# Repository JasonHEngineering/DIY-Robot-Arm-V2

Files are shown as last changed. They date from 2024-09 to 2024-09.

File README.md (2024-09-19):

## DIY Robot Arm V2
This repository is for archiving a prior 6 DOF robot project that is no longer maintained.
I am now working on the next V3 version instead. 

### Contents
| Folder  | Contents|
| --- | --- |
| [Adaptor Board](https://github.com/JasonHEngineering/DIY-Robot-Arm-V2/tree/main/Adaptor%20Board%20(schema%2C%20gerbers%2C%20kicad%20project%20folder)) | KiCad Project files. Gerber files for PCB. But no SMD assembly because for this variant of adaptor board, I did the soldering myself using both soldering iron and hot air solder. |
| [Arduino Nano](https://github.com/JasonHEngineering/DIY-Robot-Arm-V2/tree/main/Arduino%20Nano%20(.ino%20file)) | Load this file into Arduino Nano 33 BLE/IoT device. This is to be mounted into adaptor board above. |
| [CAD files](https://github.com/JasonHEngineering/DIY-Robot-Arm-V2/tree/main/CAD%20files%20(2d%2C%20step)) | Step files and 2d drawings. 2d drawings are not fully detailed; mainly the threads and tight tolerances are detailed. |
| [Raspberry Pi](https://github.com/JasonHEngineering/DIY-Robot-Arm-V2/tree/main/Raspberry%20Pi%20(plotly%20dash%20host)) | Python script and dependencies to be run on raspberry Pi 3/4 |

### Mechanical Structure
Machined CNC parts placement in assembly as shown below. 
> [!NOTE]
> In such a setup, micro limit switches can only zero the respective axis angles approximately. Next version shall use absolute encoders.    
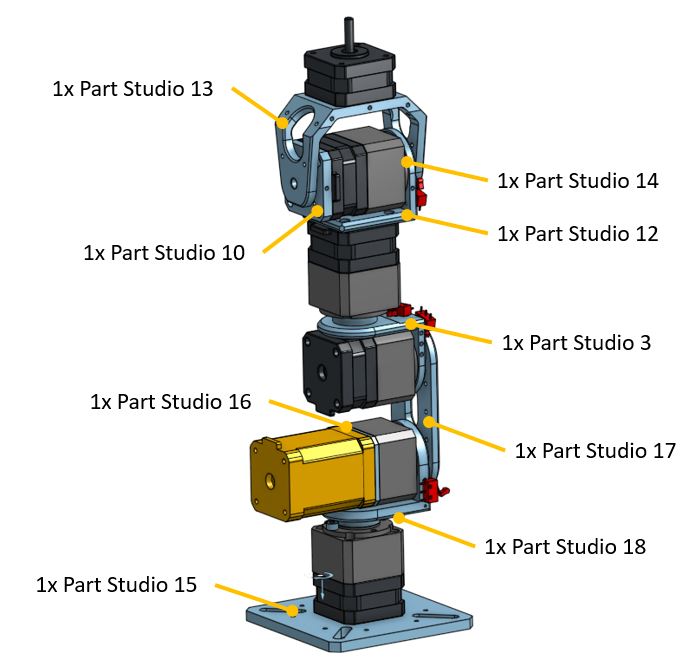
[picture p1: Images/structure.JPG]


Below illustration of user interface dealing with forward kinematics values:  
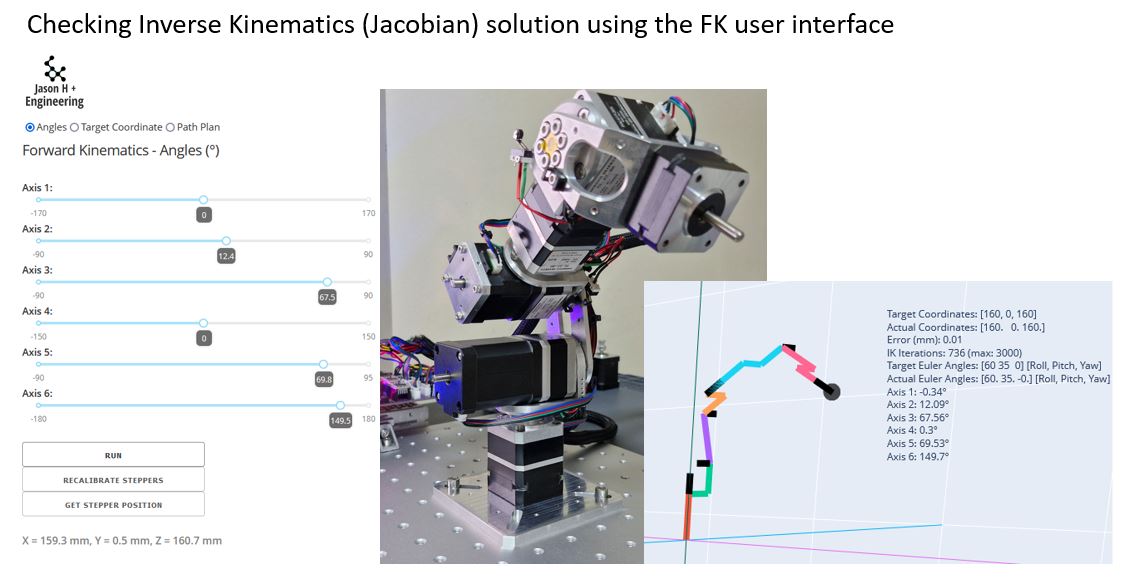
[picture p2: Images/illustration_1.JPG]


### Inverse Kinematics Solver
[Python solver](https://github.com/JasonHEngineering/Inverse-Kinematics)
1. Inverse Kinematics (CCD) – Cyclic Coordinate Descent in 3d space
2. Inverse Kinematics (vector formula Jacobian) - Euler
3. Inverse Kinematics (Numerical Jacobian) - Euler
4. Inverse Kinematics (Numerical Jacobian) - Quaternion

### Quick Illustration at YouTube
DIY Robot Arm V2 (https://www.youtube.com/watch?v=ZaQQ6-Mw-B4)

### Additional Info at WordPress
For more data/info, please refer to this [WordPress page](https://jashuang1983.wordpress.com/robotics-6-dof-arm-v2/).

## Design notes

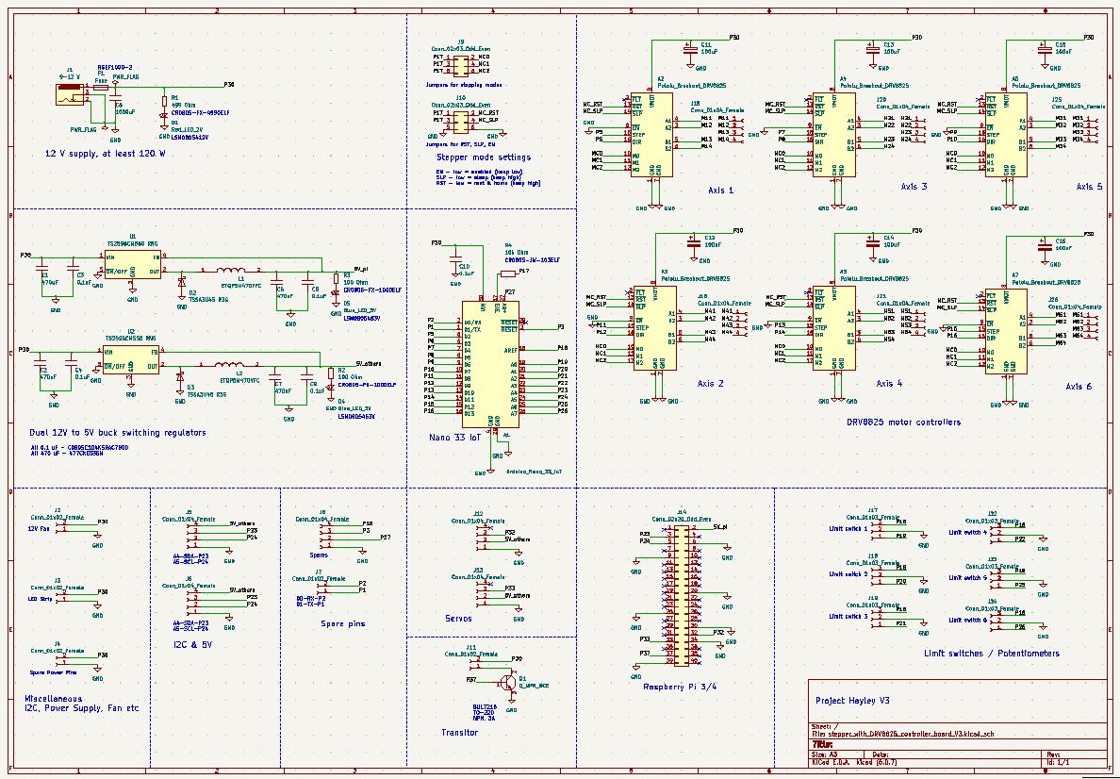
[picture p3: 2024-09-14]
Adaptor Board (schema, gerbers, kicad project folder)/schematic.JPG

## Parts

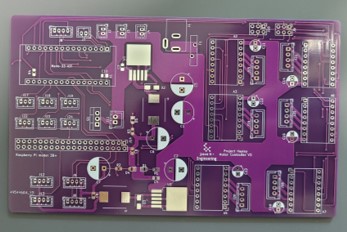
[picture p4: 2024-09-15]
Adaptor Board (schema, gerbers, kicad project folder)/without_components.jpg

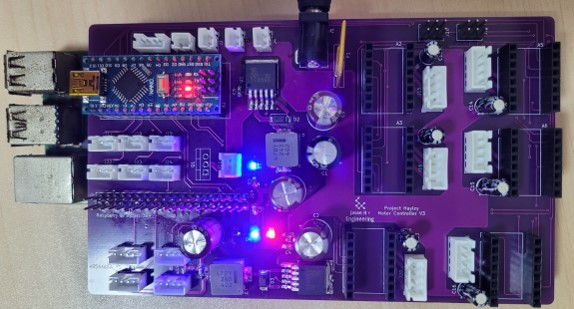
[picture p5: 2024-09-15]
Adaptor Board (schema, gerbers, kicad project folder)/with_components_mounted.jpg

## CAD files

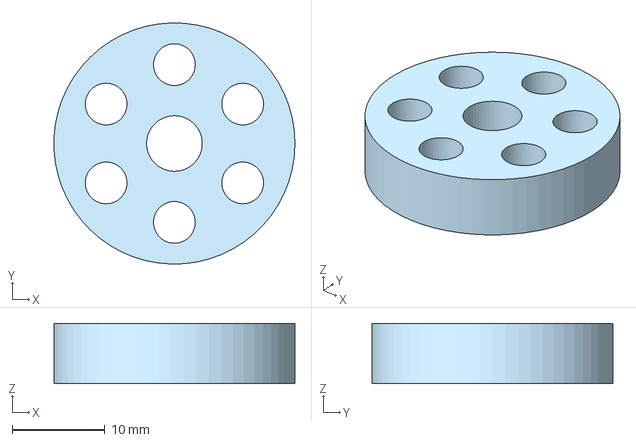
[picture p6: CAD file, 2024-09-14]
CAD files (2d, step)/Part 14.step
26.0 x 26.0 x 6.50 mm

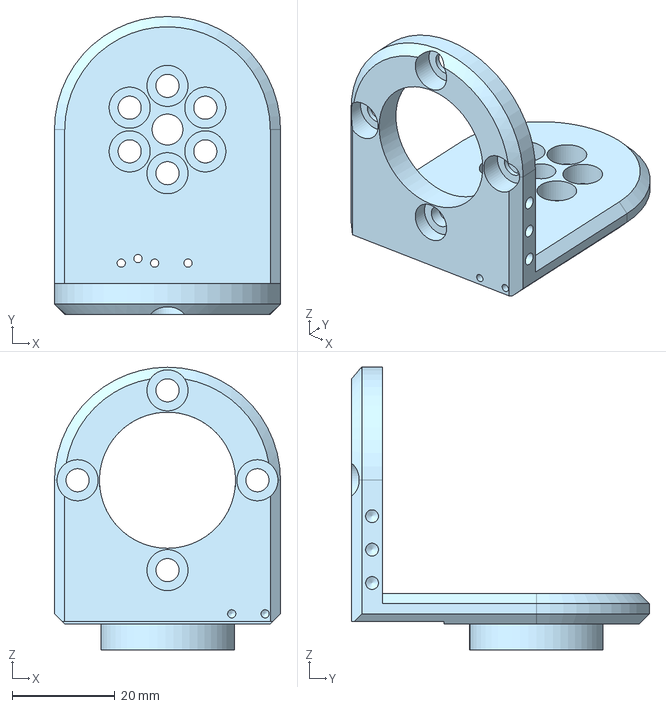
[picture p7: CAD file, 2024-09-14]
CAD files (2d, step)/Part 3.step
44.0 x 58.0 x 55.0 mm

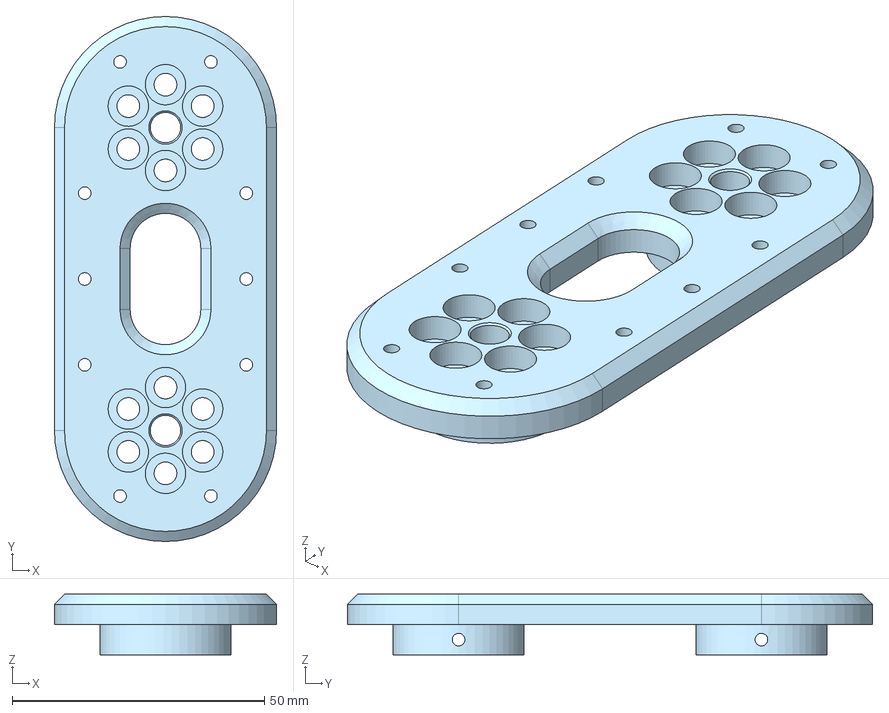
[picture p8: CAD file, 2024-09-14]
CAD files (2d, step)/Part 17.step
44.0 x 104.0 x 12.0 mm

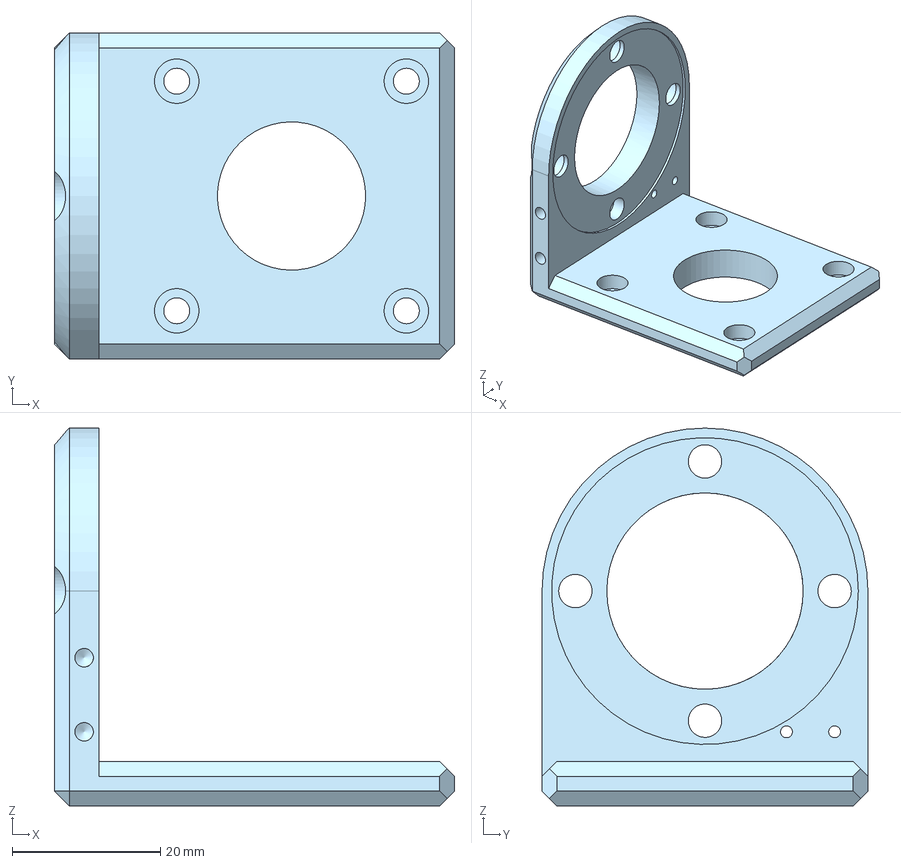
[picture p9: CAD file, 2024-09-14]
CAD files (2d, step)/Part 12.step
54.0 x 44.0 x 51.0 mm

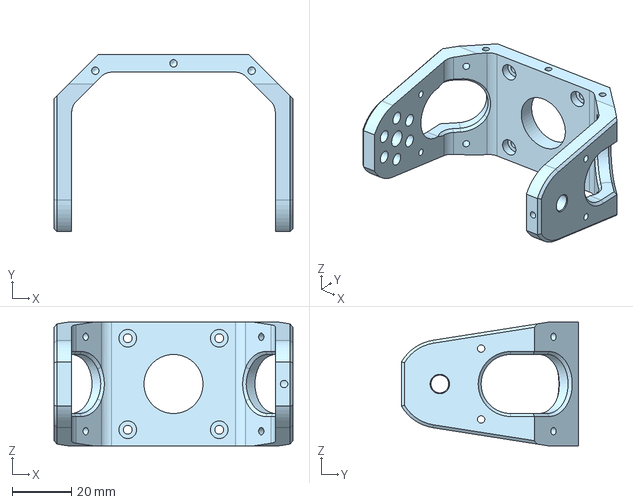
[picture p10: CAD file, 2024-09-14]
CAD files (2d, step)/Part 13.step
81.0 x 60.0 x 42.0 mm

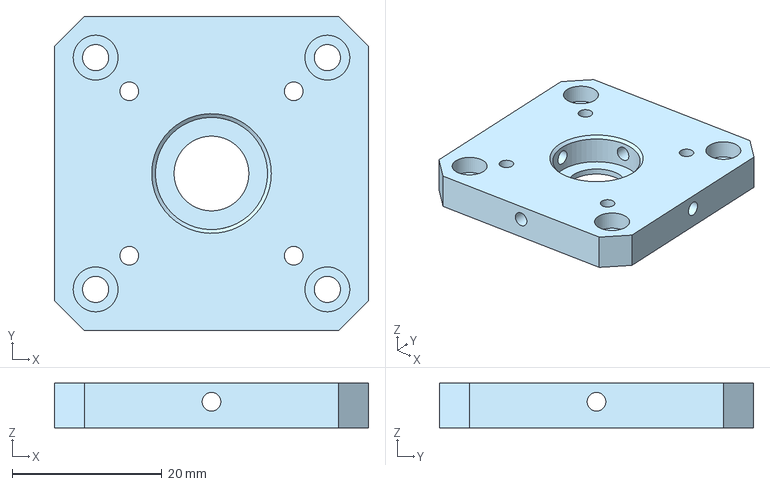
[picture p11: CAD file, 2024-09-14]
CAD files (2d, step)/Part 10.step
42.0 x 42.0 x 6.00 mm

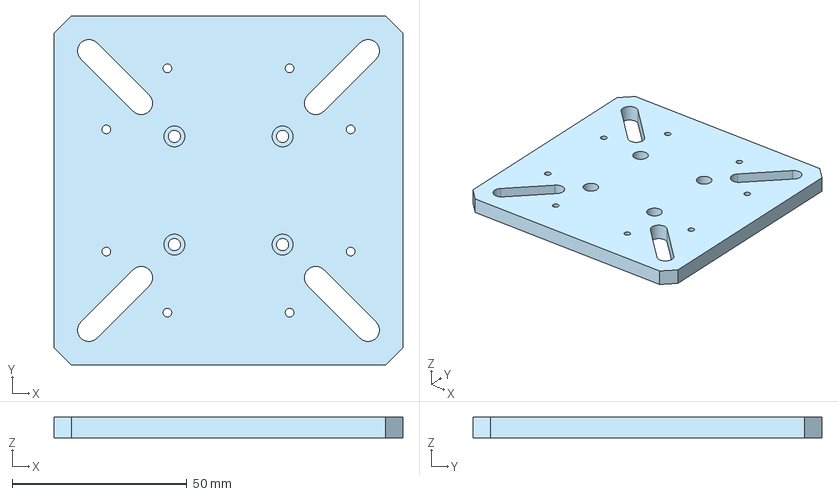
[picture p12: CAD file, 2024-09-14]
CAD files (2d, step)/Part 15.step
100.0 x 100.0 x 6.00 mm

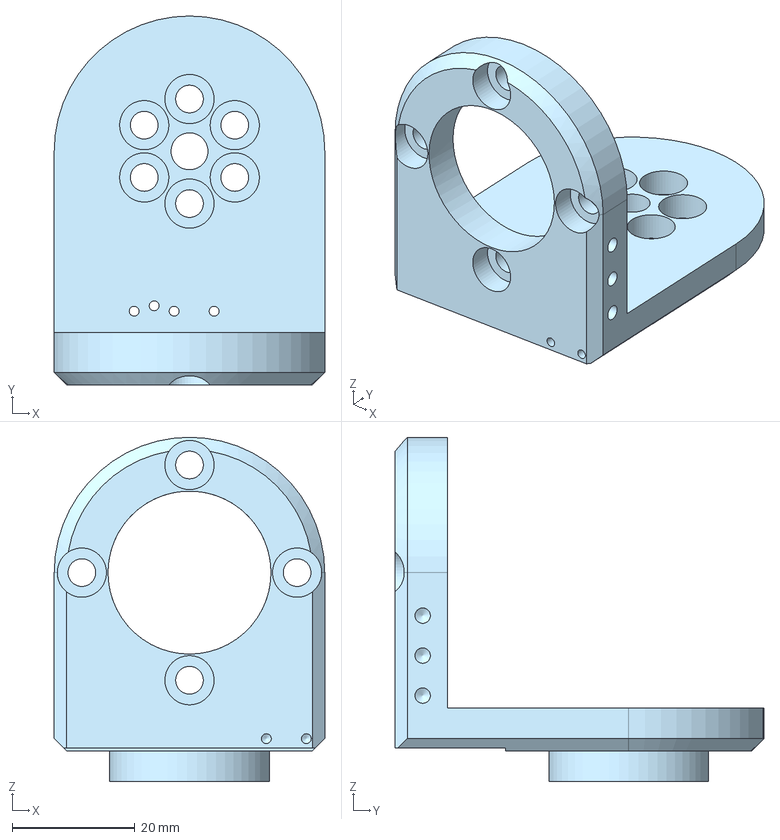
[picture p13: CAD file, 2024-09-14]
CAD files (2d, step)/Part 18.step
44.0 x 60.0 x 56.0 mm

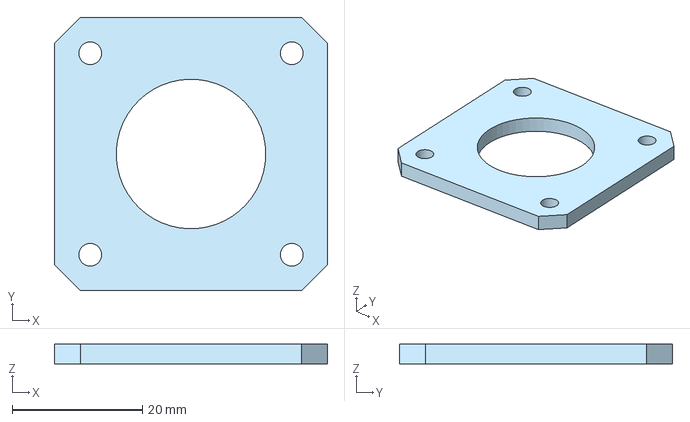
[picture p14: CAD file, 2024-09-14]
CAD files (2d, step)/Part 16.step
42.0 x 42.0 x 3.00 mm

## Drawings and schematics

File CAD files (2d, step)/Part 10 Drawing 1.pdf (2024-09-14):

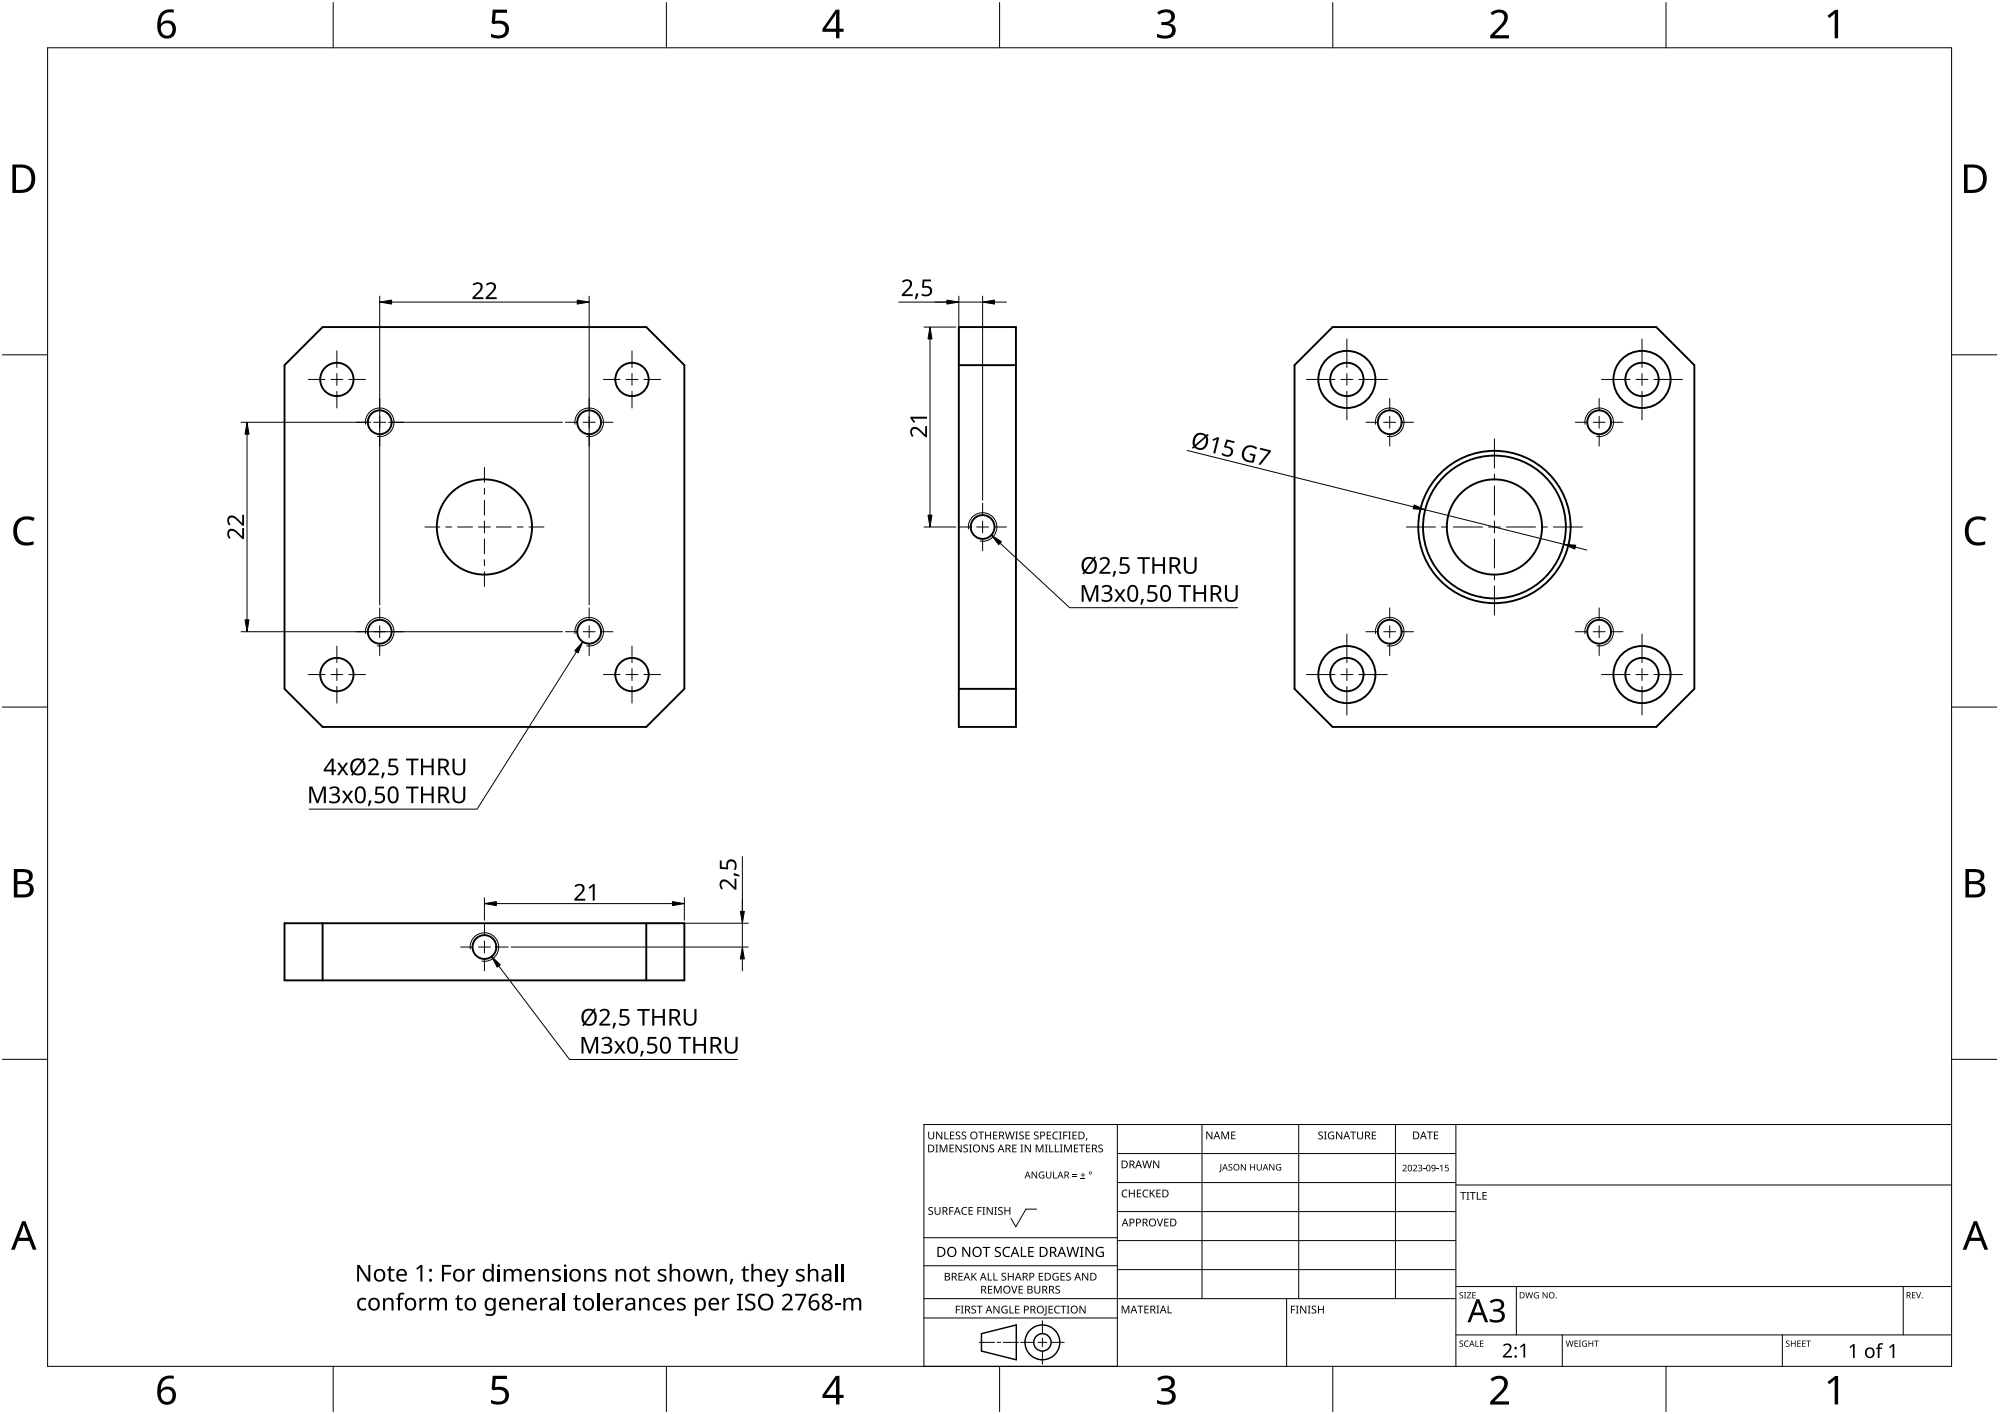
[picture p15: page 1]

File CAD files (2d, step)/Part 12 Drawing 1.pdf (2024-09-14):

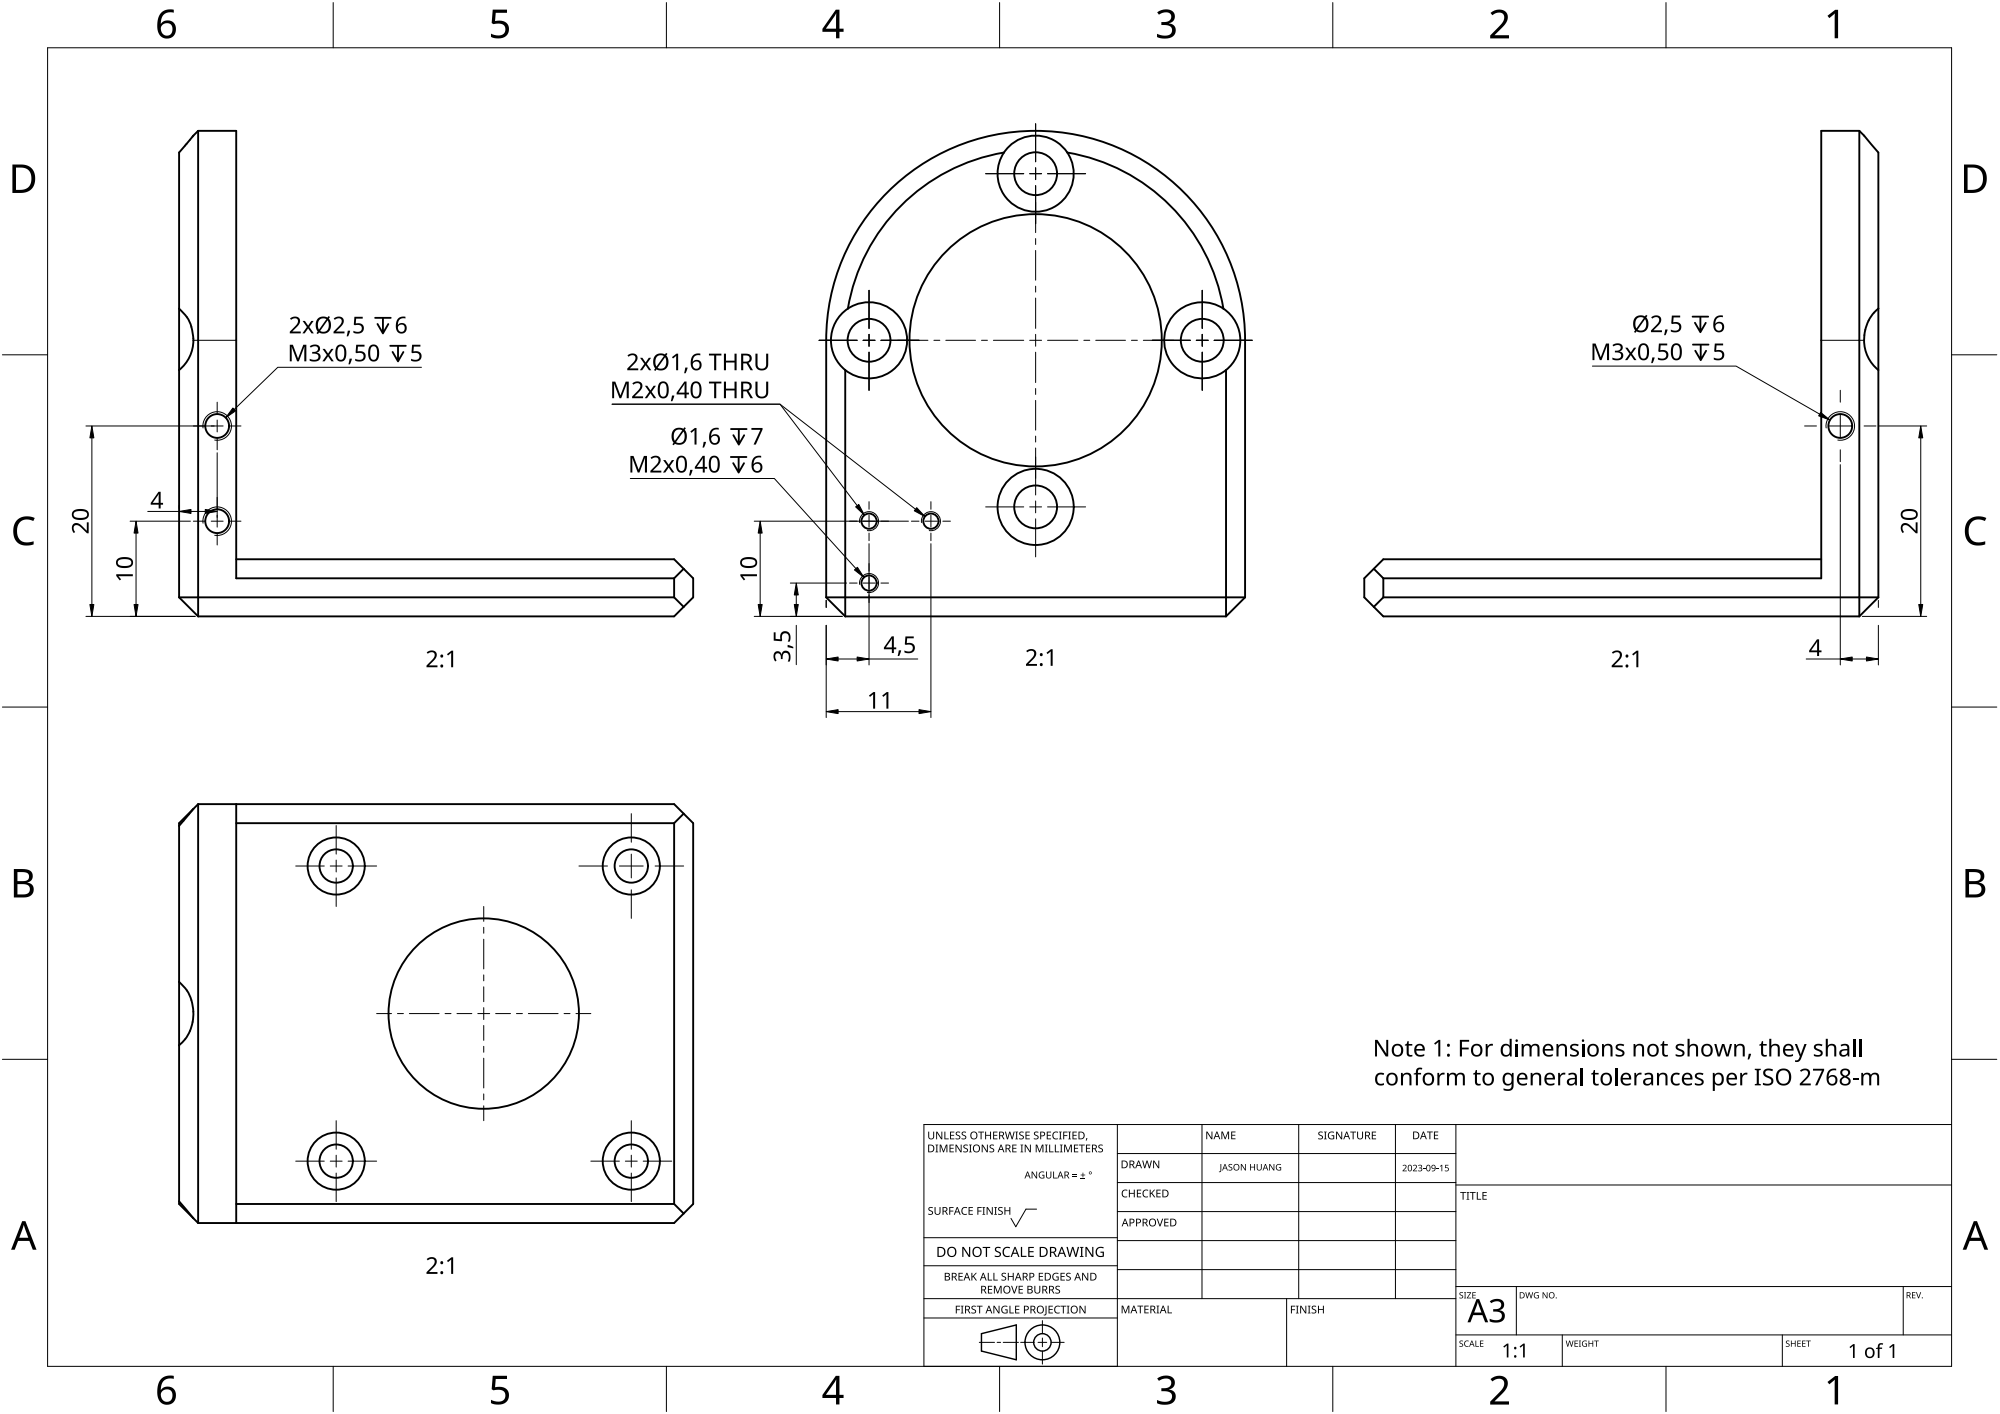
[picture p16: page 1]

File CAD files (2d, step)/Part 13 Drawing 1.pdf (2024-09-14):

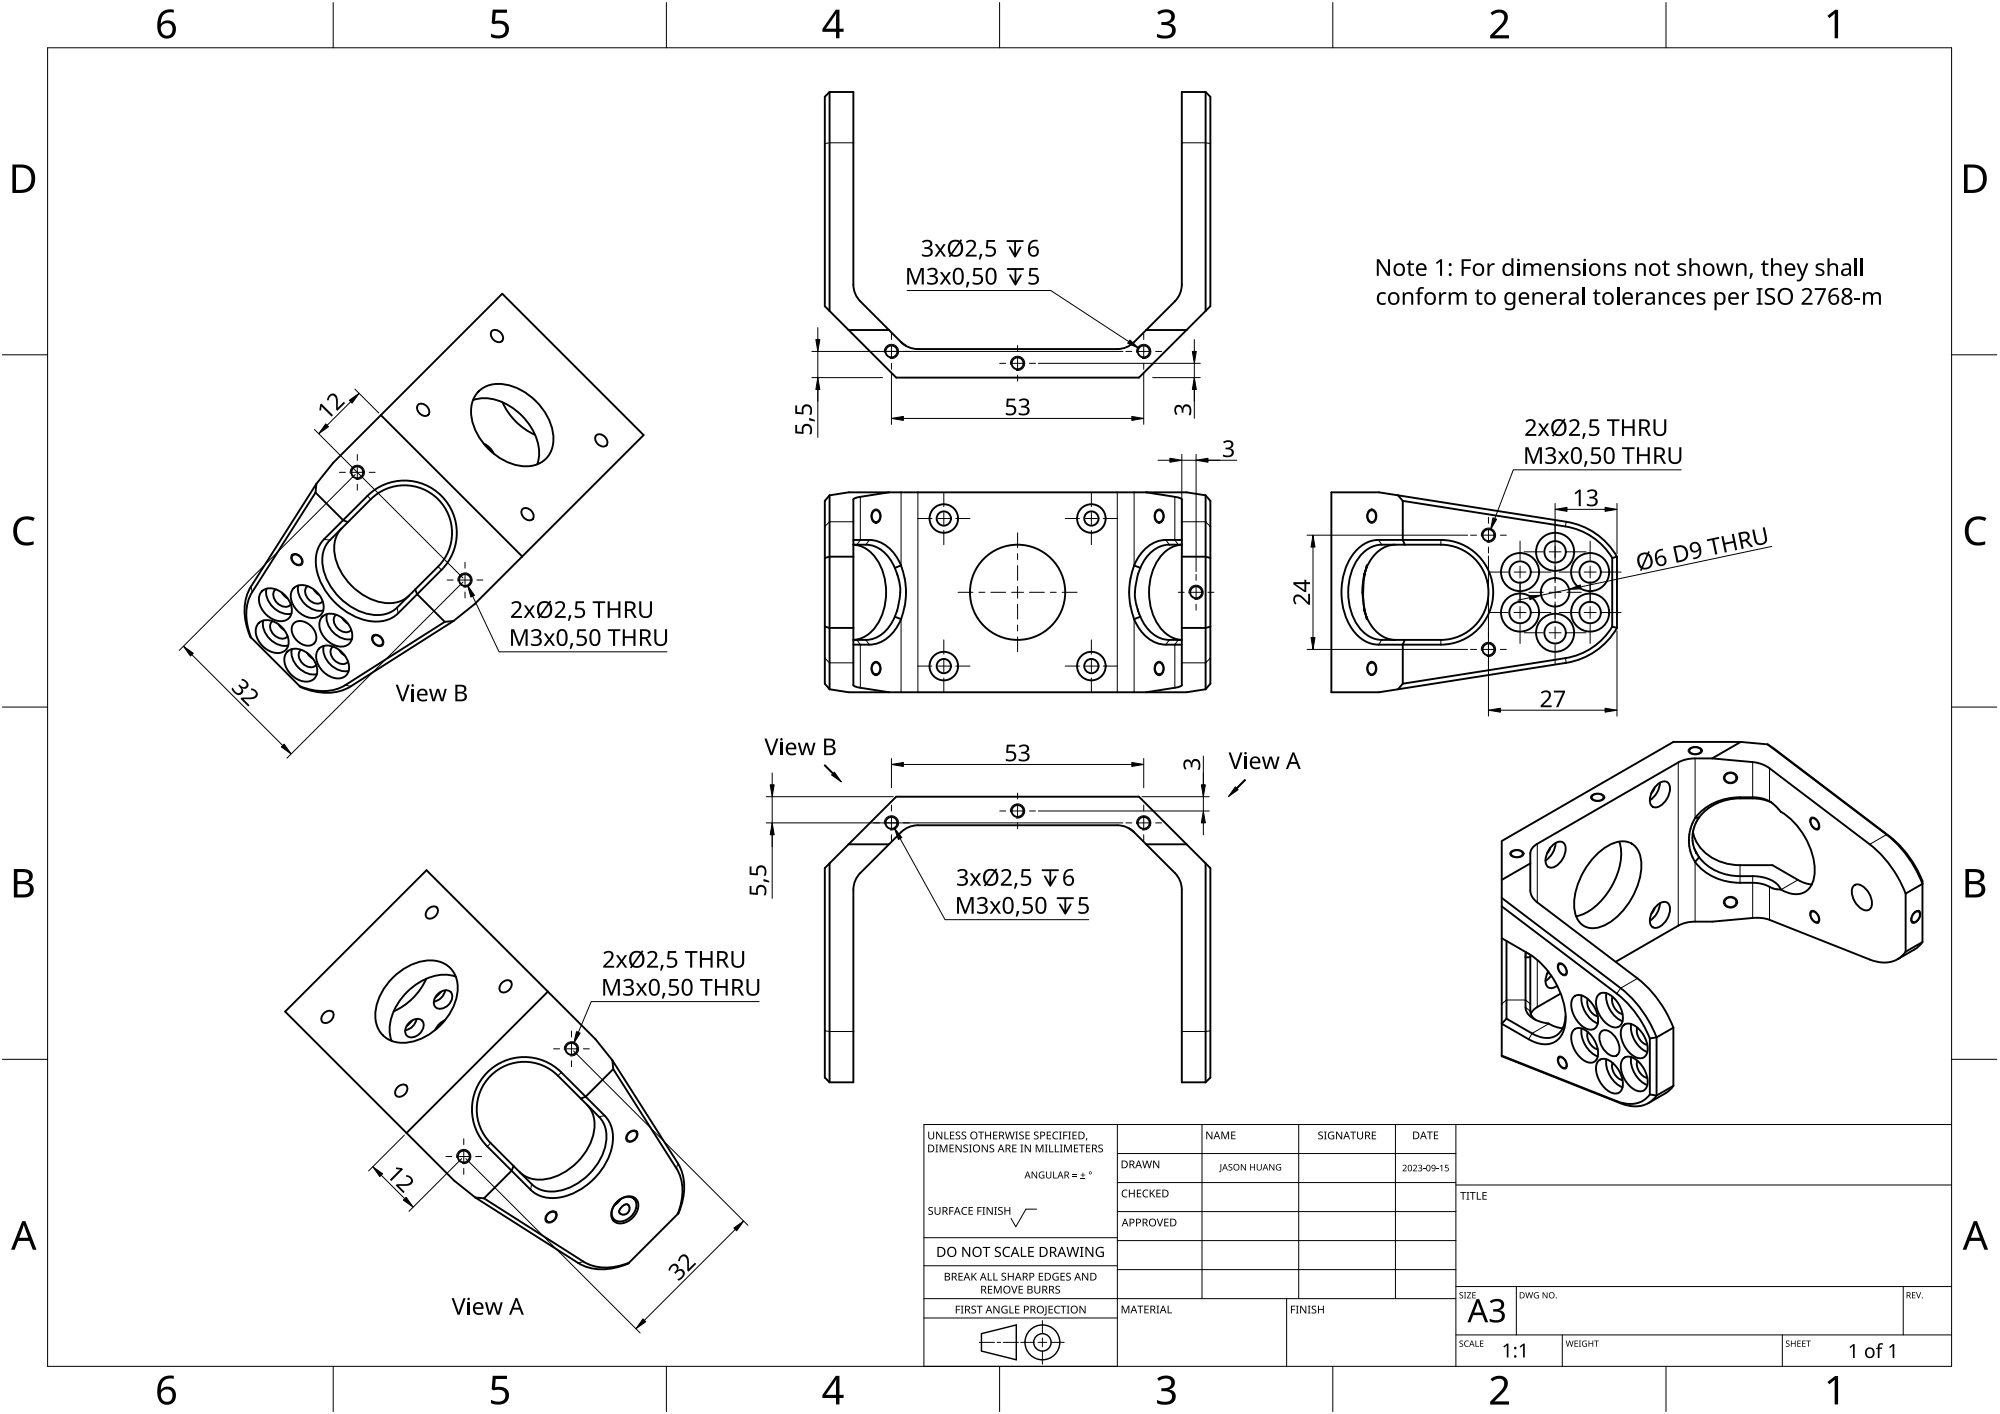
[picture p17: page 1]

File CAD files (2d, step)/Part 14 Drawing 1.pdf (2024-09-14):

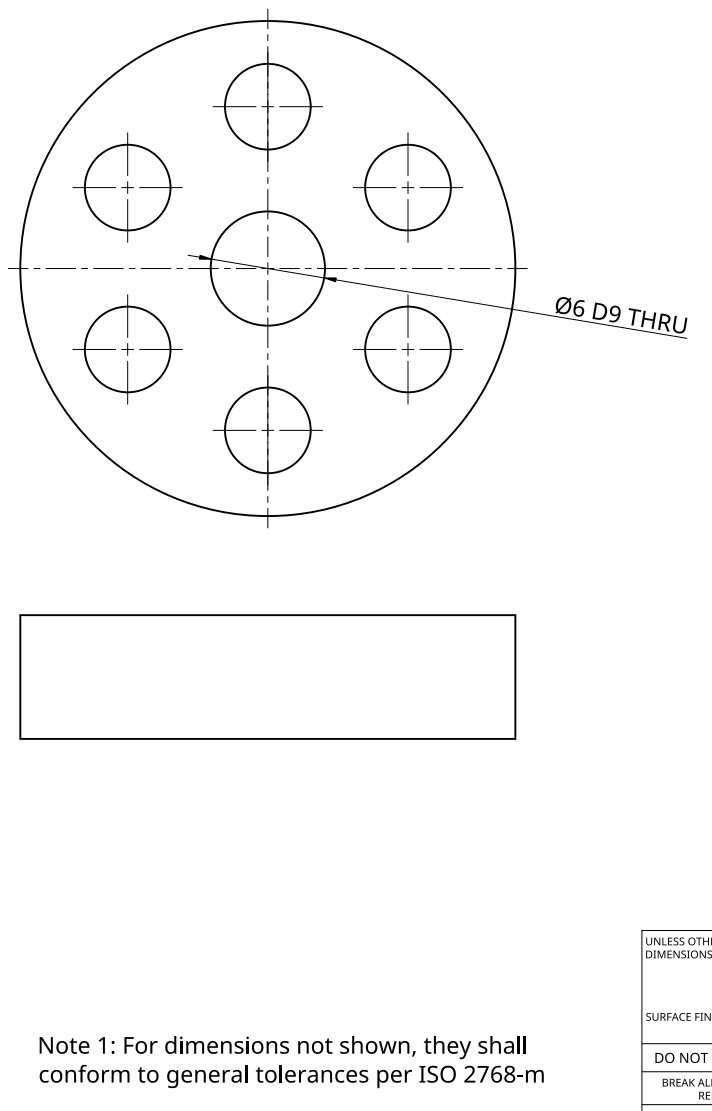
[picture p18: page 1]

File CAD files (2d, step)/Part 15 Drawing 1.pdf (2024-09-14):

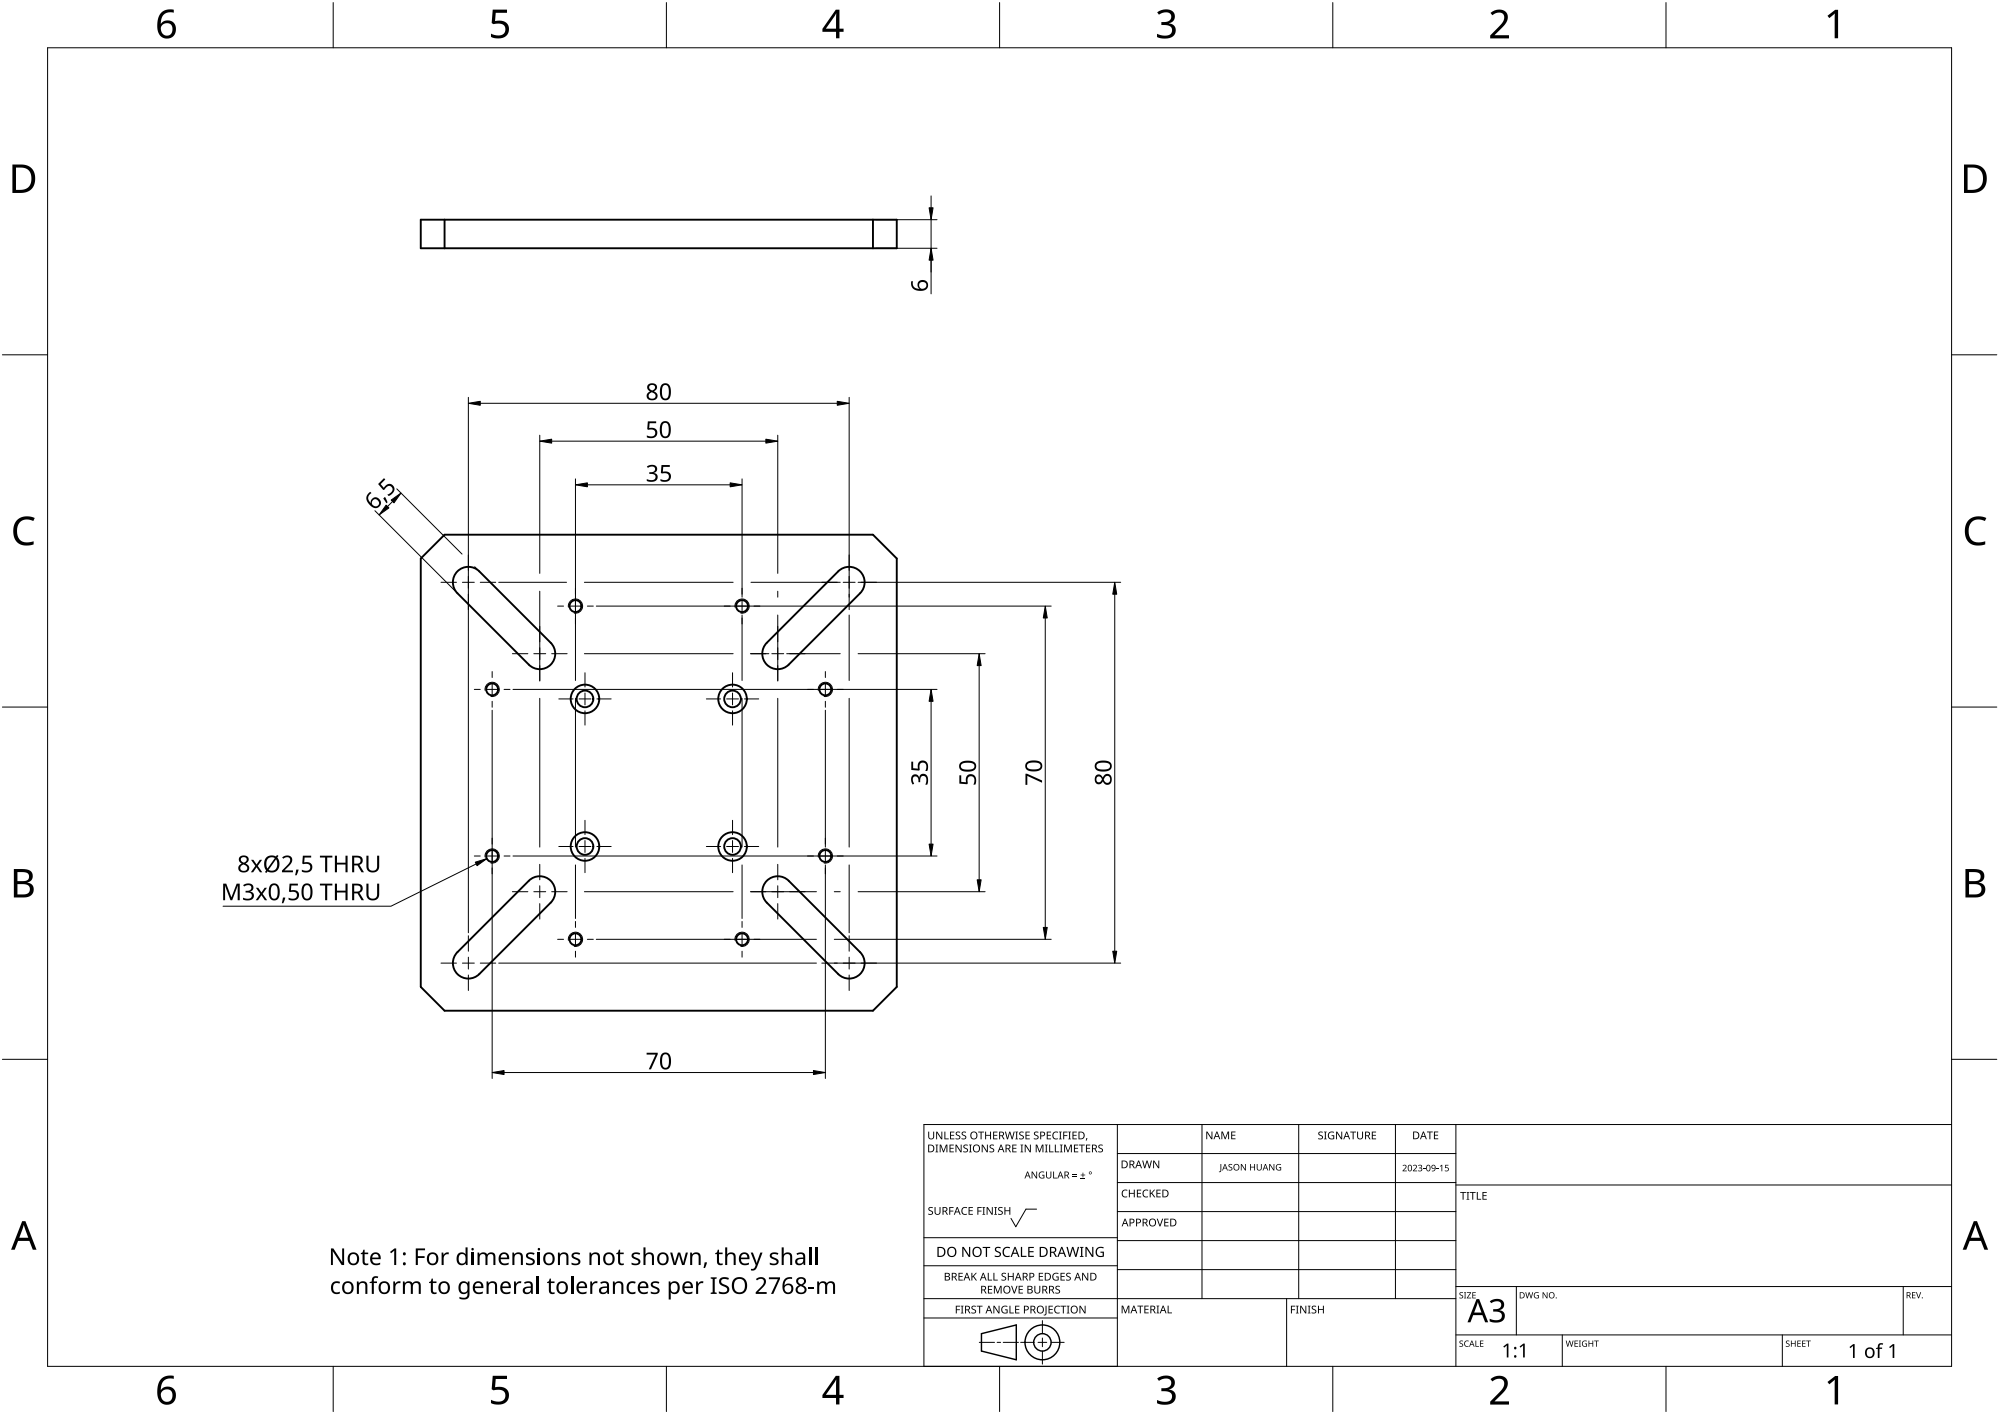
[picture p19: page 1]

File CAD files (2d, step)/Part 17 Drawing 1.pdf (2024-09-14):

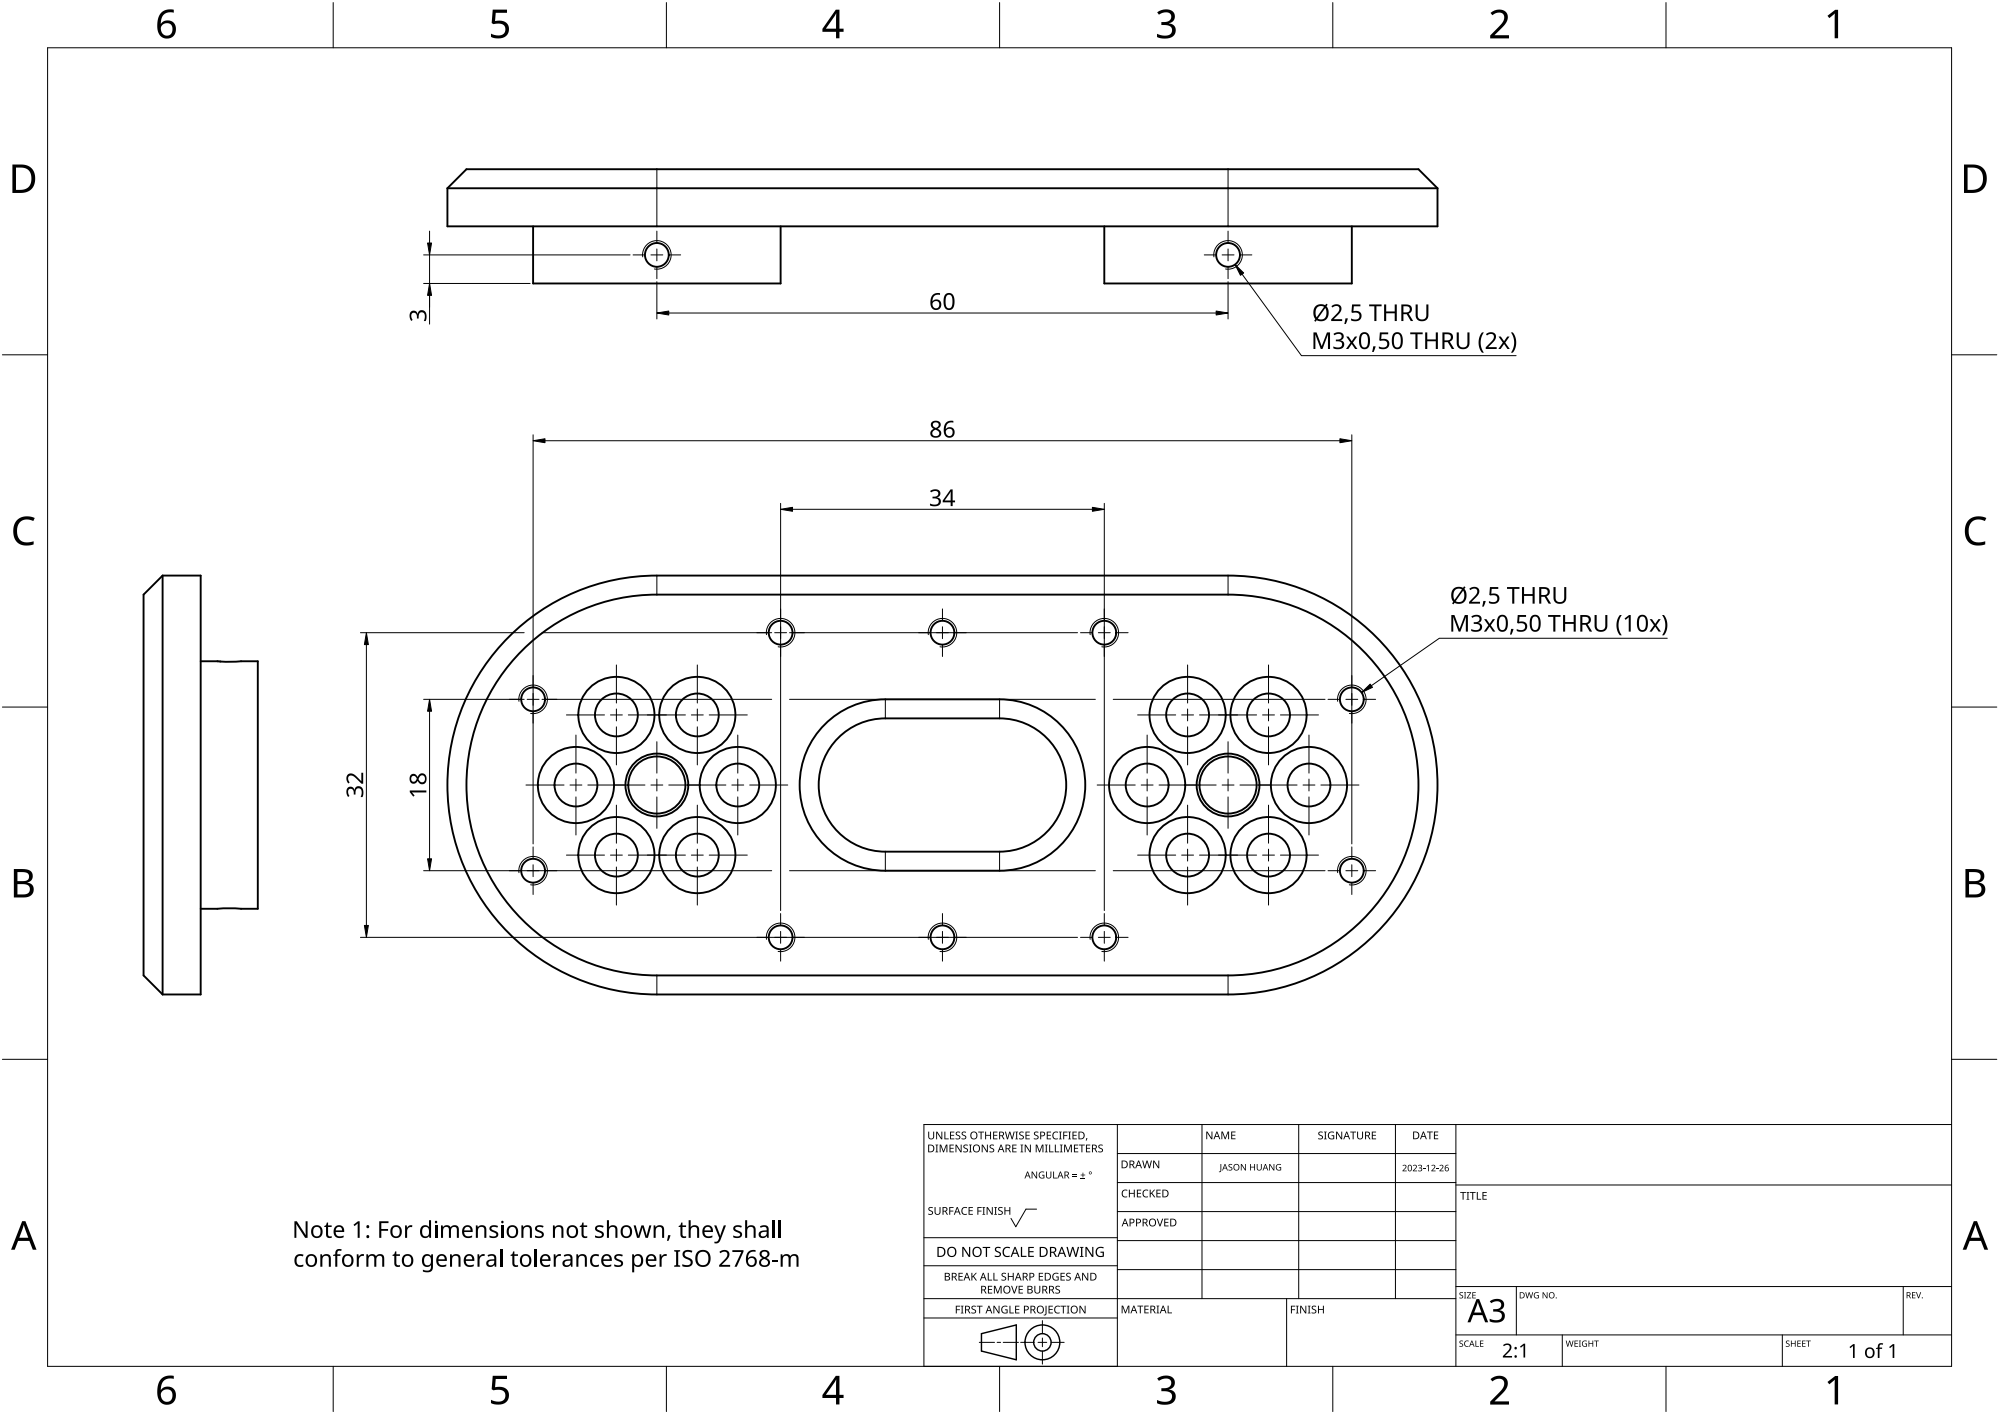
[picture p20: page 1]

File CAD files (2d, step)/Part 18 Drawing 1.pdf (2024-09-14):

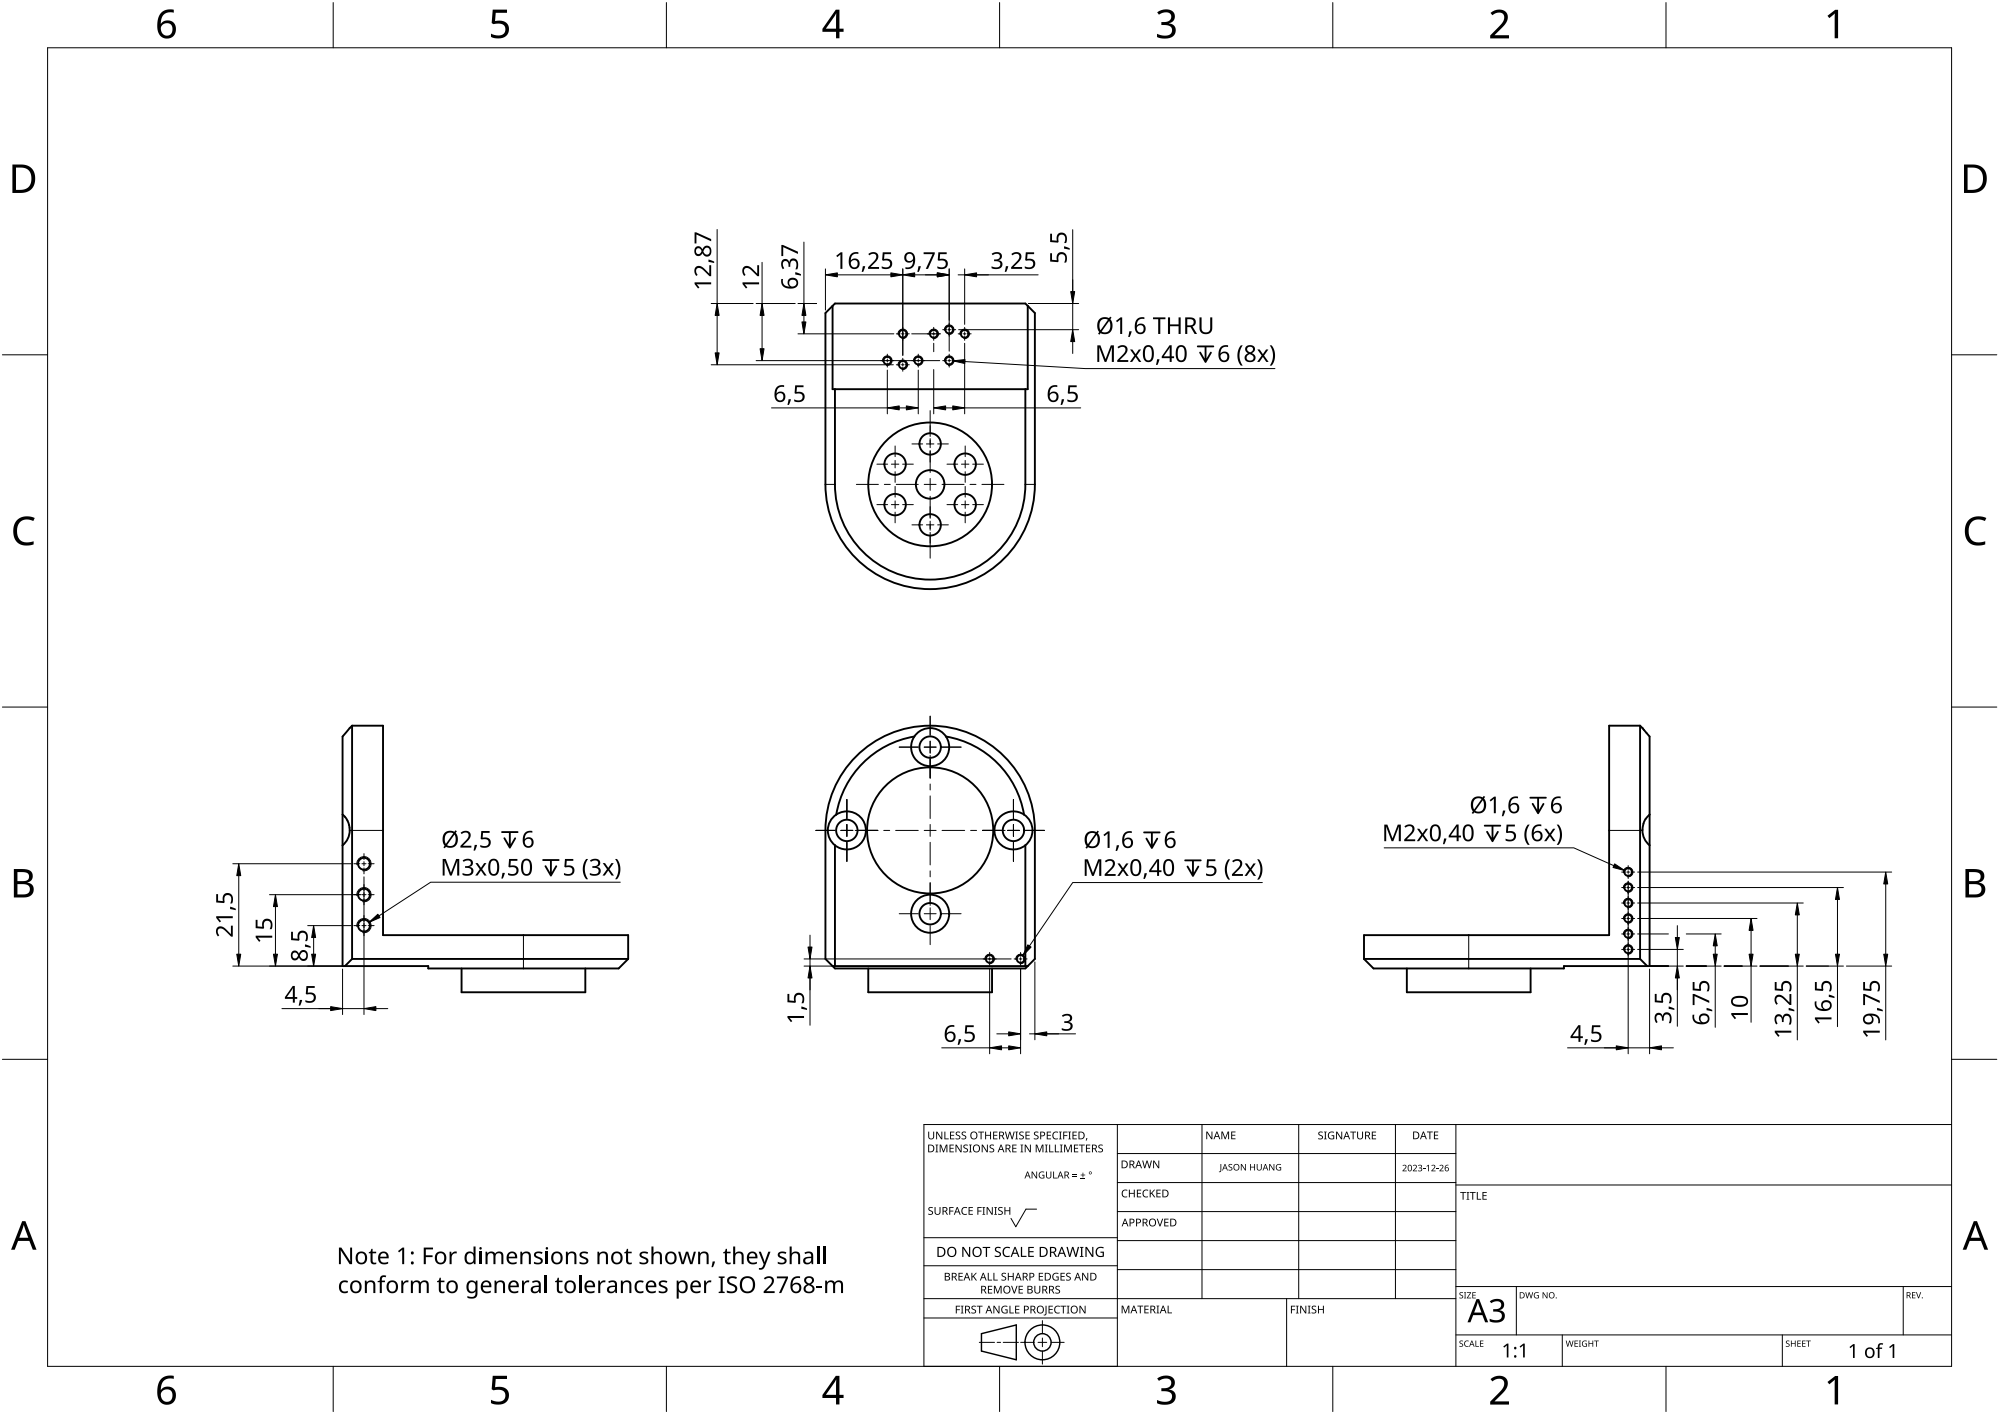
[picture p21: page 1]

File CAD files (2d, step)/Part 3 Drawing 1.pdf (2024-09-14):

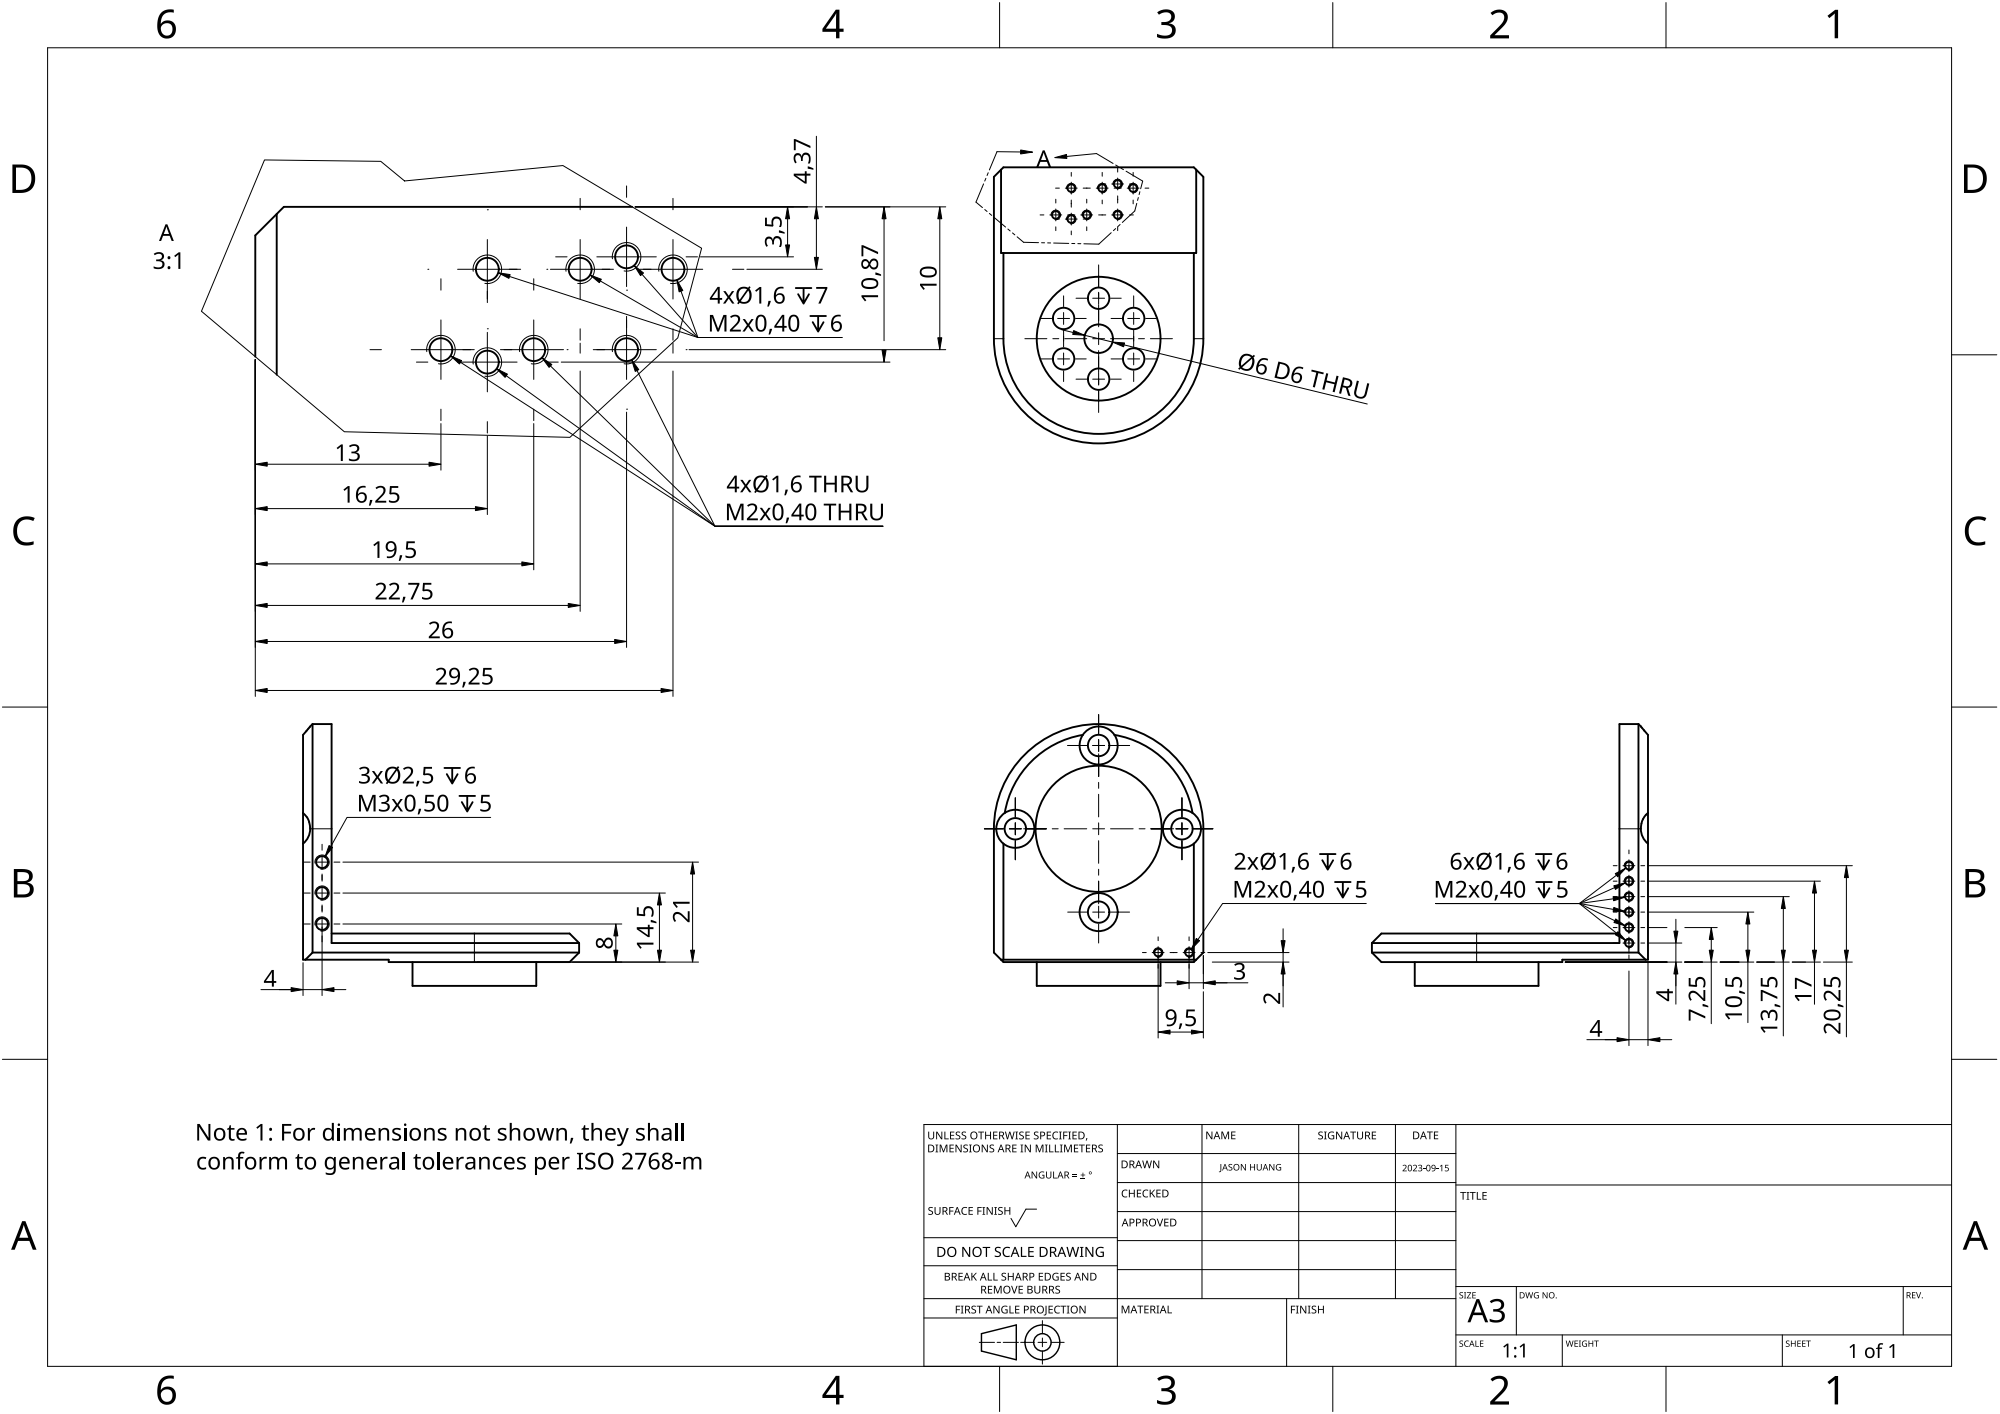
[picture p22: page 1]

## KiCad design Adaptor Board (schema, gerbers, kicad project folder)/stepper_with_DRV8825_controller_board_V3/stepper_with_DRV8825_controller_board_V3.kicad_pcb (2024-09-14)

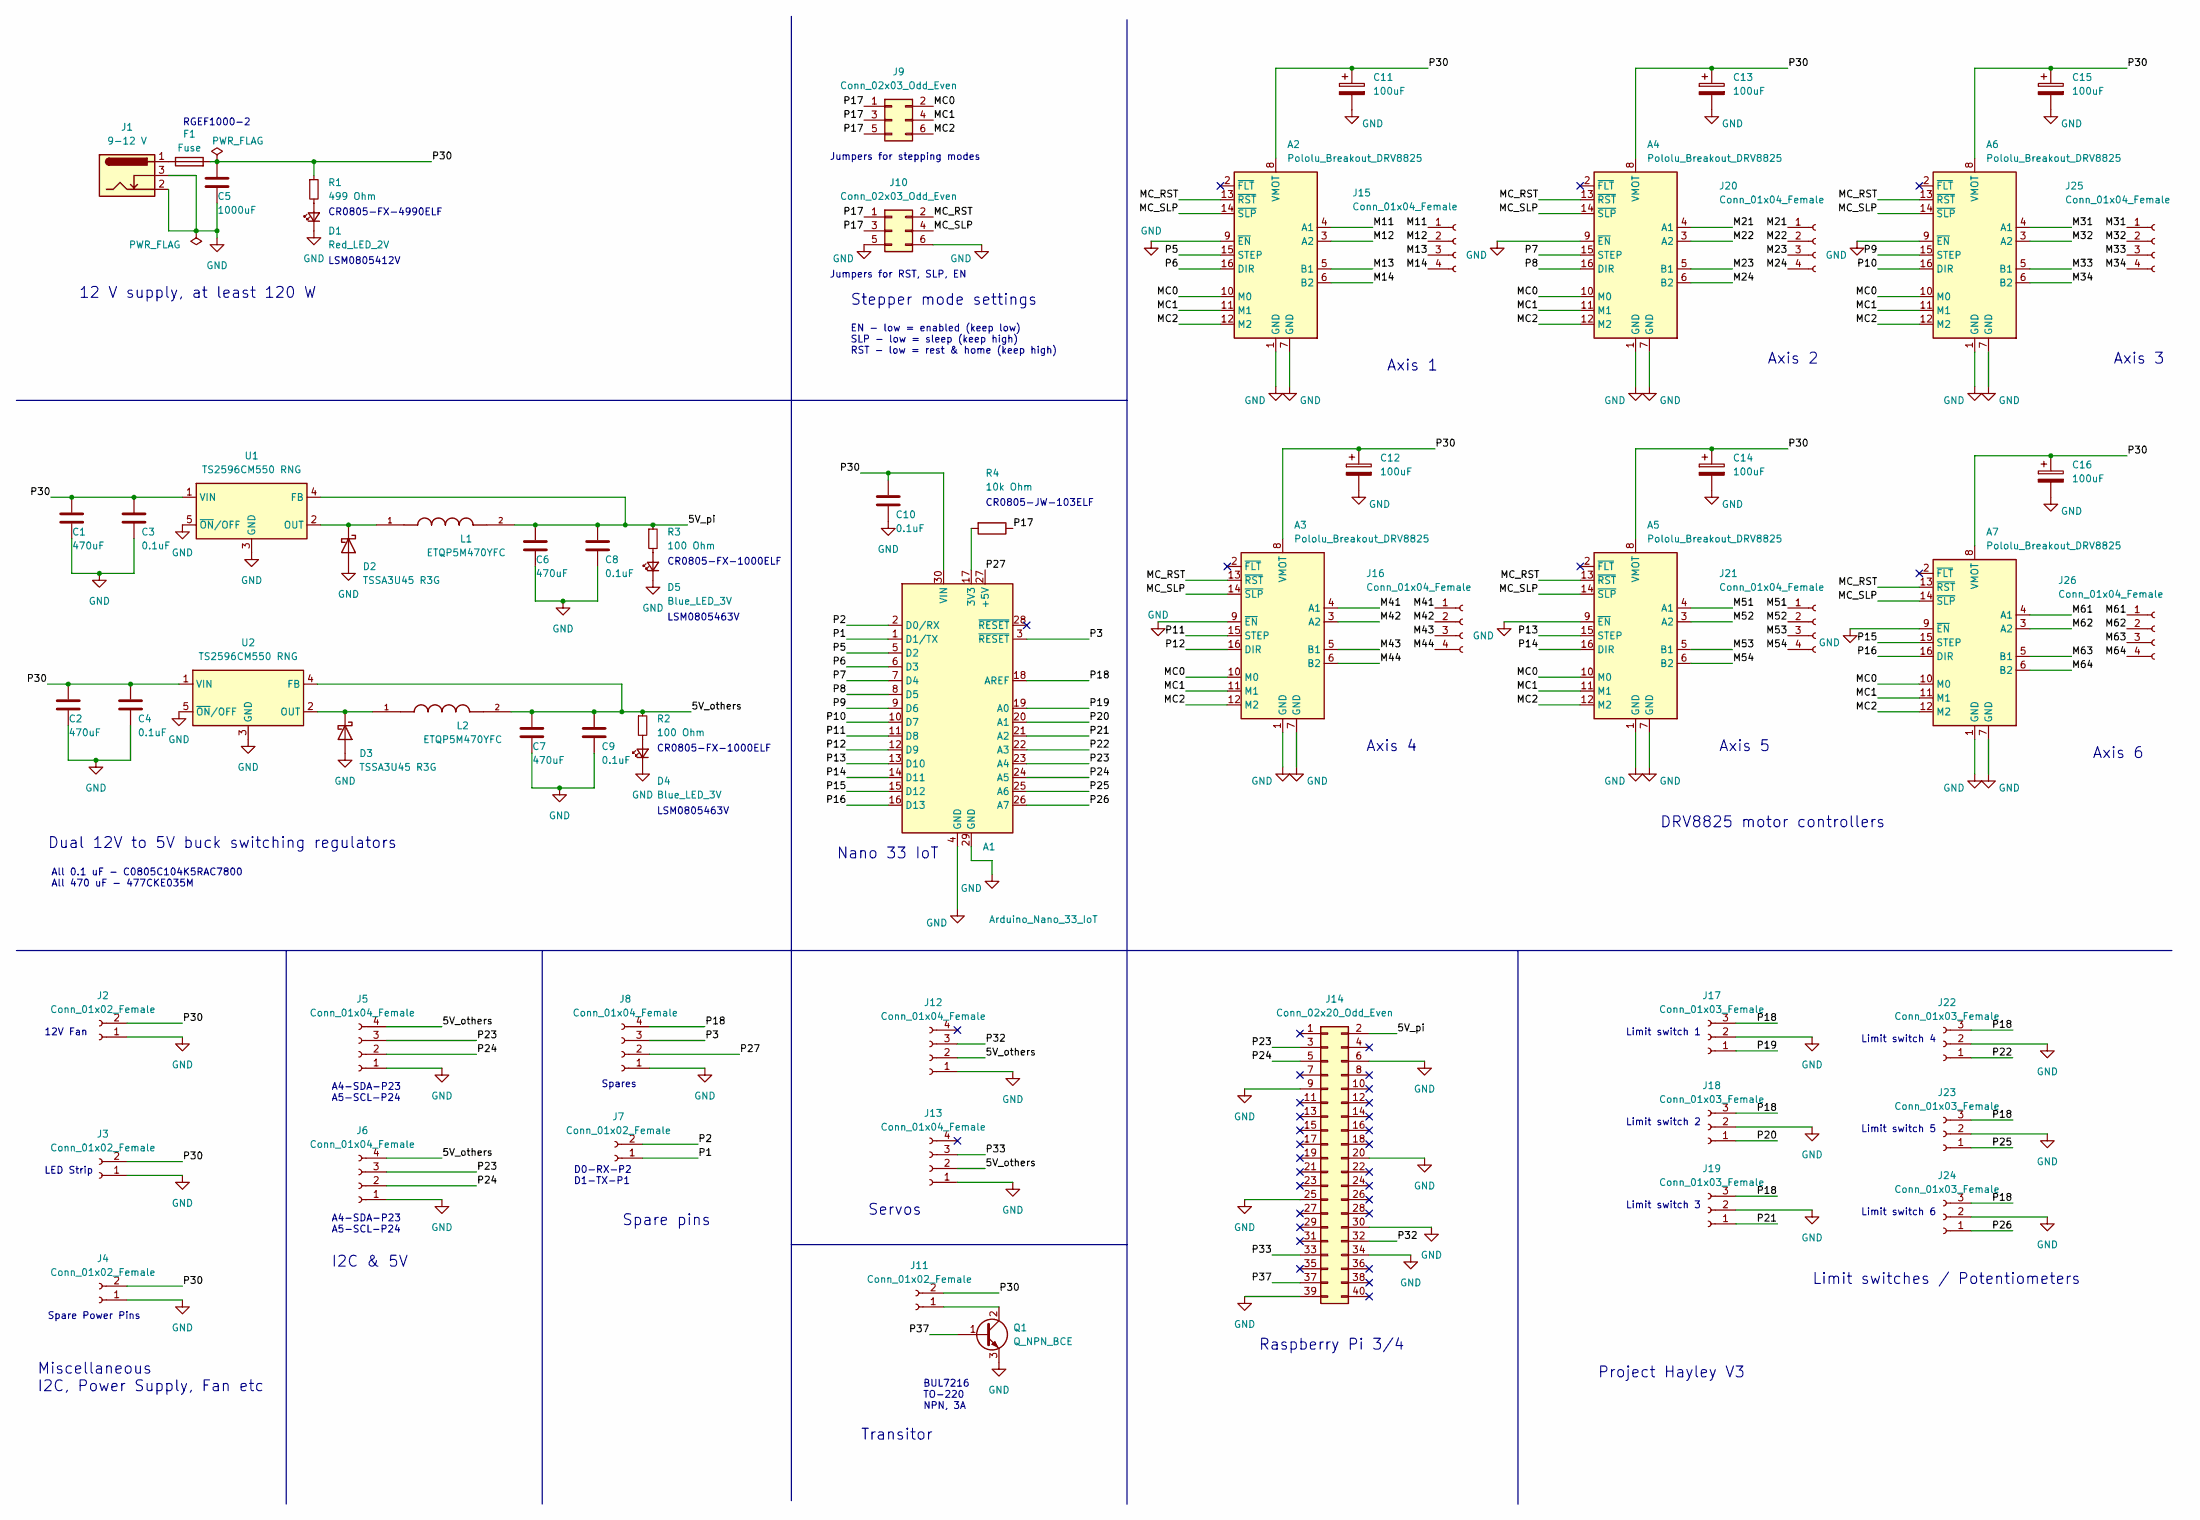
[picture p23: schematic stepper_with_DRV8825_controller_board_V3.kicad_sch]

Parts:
A1: Arduino_Nano_33_IoT; Arduino_Nano
A2, A3, A4, A5, A6, A7: Pololu_Breakout_DRV8825; Pololu_Breakout-16_15.2x20.3mm
C1, C2, C6, C7: 470uF; CP_Radial_D10.0mm_P5.00mm
C3, C4, C8, C9, C10: 0.1uF; C_0805_2012Metric_Pad1.18x1.45mm_HandSolder
C5: 1000uF; CP_Radial_D10.0mm_P5.00mm
C11, C12, C13, C14, C15, C16: 100uF; CP_Radial_D5.0mm_P2.50mm
D1: Red_LED_2V; LED_0805_2012Metric_Pad1.15x1.40mm_HandSolder
D2, D3: TSSA3U45 R3G; D_SMA
D4, D5: Blue_LED_3V; LED_0805_2012Metric_Pad1.15x1.40mm_HandSolder
F1: Fuse; FUSRB510W81L1358T310H1980
J1: 9-12 V; NINIGI_DC-005
J2, J3, J4, J7: Conn_01x02_Female; JST_PH_B2B-PH-K_1x02_P2.00mm_Vertical
J5, J6, J8, J12, J13: Conn_01x04_Female; JST_PH_B4B-PH-K_1x04_P2.00mm_Vertical
J9, J10: Conn_02x03_Odd_Even; PinHeader_2x03_P2.54mm_Vertical
J11: Conn_01x02_Female; JST_XH_B2B-XH-A_1x02_P2.50mm_Vertical
J14: Conn_02x20_Odd_Even; PinHeader_2x20_P2.54mm_Vertical
J15, J16, J20, J21, J25, J26: Conn_01x04_Female; JST_XH_B4B-XH-A_1x04_P2.50mm_Vertical
J17, J18, J19, J22, J23, J24: Conn_01x03_Female; JST_PH_B3B-PH-K_1x03_P2.00mm_Vertical
L1, L2: ETQP5M470YFC; IND_ETQP5M470YFC; PARTREV 1-Feb-20
Q1: Q_NPN_BCE; TO-220-3_Vertical
R1: 499 Ohm; R_0805_2012Metric_Pad1.20x1.40mm_HandSolder
R2, R3: 100 Ohm; R_0805_2012Metric_Pad1.20x1.40mm_HandSolder
R4: 10k Ohm; R_0805_2012Metric_Pad1.20x1.40mm_HandSolder
U1, U2: TS2596CM550 RNG; TO-263-5_TabPin3

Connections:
/5V_others: C7.1, C9.1, J5.4, J6.4, J12.2, J13.2, L2.2, R2.1, U2.4 (FB)
/5V_pi: C6.1, C8.1, J14.2, L1.2, R3.1, U1.4 (FB)
/M11: A2.4 (A1), J15.1
/M12: A2.3 (A2), J15.2
/M13: A2.5 (B1), J15.3
/M14: A2.6 (B2), J15.4
/M21: A4.4 (A1), J20.1
/M22: A4.3 (A2), J20.2
/M23: A4.5 (B1), J20.3
/M24: A4.6 (B2), J20.4
/M31: A6.4 (A1), J25.1
/M32: A6.3 (A2), J25.2
/M33: A6.5 (B1), J25.3
/M34: A6.6 (B2), J25.4
/M41: A3.4 (A1), J16.1
/M42: A3.3 (A2), J16.2
/M43: A3.5 (B1), J16.3
/M44: A3.6 (B2), J16.4
/M51: A5.4 (A1), J21.1
/M52: A5.3 (A2), J21.2
/M53: A5.5 (B1), J21.3
/M54: A5.6 (B2), J21.4
/M61: A7.4 (A1), J26.1
/M62: A7.3 (A2), J26.2
/M63: A7.5 (B1), J26.3
/M64: A7.6 (B2), J26.4
/MC0: A2.10 (M0), A3.10 (M0), A4.10 (M0), A5.10 (M0), A6.10 (M0), A7.10 (M0), J9.2
/MC1: A2.11 (M1), A3.11 (M1), A4.11 (M1), A5.11 (M1), A6.11 (M1), A7.11 (M1), J9.4
/MC2: A2.12 (M2), A3.12 (M2), A4.12 (M2), A5.12 (M2), A6.12 (M2), A7.12 (M2), J9.6
/MC_RST: A2.13 (~RST), A3.13 (~RST), A4.13 (~RST), A5.13 (~RST), A6.13 (~RST), A7.13 (~RST), J10.2
/MC_SLP: A2.14 (~SLP), A3.14 (~SLP), A4.14 (~SLP), A5.14 (~SLP), A6.14 (~SLP), A7.14 (~SLP), J10.4
/P1: A1.1 (D1/TX), J7.1
/P2: A1.2 (D0/RX), J7.2
/P3: A1.3 (~RESET), J8.3
/P5: A1.5 (D2), A2.15 (STEP)
/P6: A1.6 (D3), A2.16 (DIR)
/P7: A1.7 (D4), A4.15 (STEP)
/P8: A1.8 (D5), A4.16 (DIR)
/P9: A1.9 (D6), A6.15 (STEP)
/P10: A1.10 (D7), A6.16 (DIR)
/P11: A1.11 (D8), A3.15 (STEP)
/P12: A1.12 (D9), A3.16 (DIR)
/P13: A1.13 (D10), A5.15 (STEP)
/P14: A1.14 (D11), A5.16 (DIR)
/P15: A1.15 (D12), A7.15 (STEP)
/P16: A1.16 (D13), A7.16 (DIR)
/P17: J9.1, J9.3, J9.5, J10.1, J10.3, R4.1
/P18: A1.18 (AREF), J8.4, J17.3, J18.3, J19.3, J22.3, J23.3, J24.3
/P19: A1.19 (A0), J17.1
/P20: A1.20 (A1), J18.1
/P21: A1.21 (A2), J19.1
/P22: A1.22 (A3), J22.1
/P23: A1.23 (A4), J5.3, J6.3, J14.3
/P24: A1.24 (A5), J5.2, J6.2, J14.5
/P25: A1.25 (A6), J23.1
/P26: A1.26 (A7), J24.1
/P27: A1.27 (+5V), J8.2
/P30: A1.30 (VIN), A2.8 (VMOT), A3.8 (VMOT), A4.8 (VMOT), A5.8 (VMOT), A6.8 (VMOT), A7.8 (VMOT), C1.1, C2.1, C3.1, C4.1, C5.1, C10.1, C11.1, C12.1, C13.1, C14.1, C15.1, C16.1, F1.2, J2.2, J3.2, J4.2, J11.2, R1.1, U1.1 (VIN), U2.1 (VIN)
/P32: J12.3, J14.32
/P33: J13.3, J14.33
/P37: J14.37, Q1.1 (B)
GND: A1.4 (GND), A1.29 (GND), A2.1 (GND), A2.7 (GND), A2.9 (~EN), A3.1 (GND), A3.7 (GND), A3.9 (~EN), A4.1 (GND), A4.7 (GND), A4.9 (~EN), A5.1 (GND), A5.7 (GND), A5.9 (~EN), A6.1 (GND), A6.7 (GND), A6.9 (~EN), A7.1 (GND), A7.7 (GND), A7.9 (~EN), C1.2, C2.2, C3.2, C4.2, C5.2, C6.2, C7.2, C8.2, C9.2, C10.2, C11.2, C12.2, C13.2, C14.2, C15.2, C16.2, D1.1 (K), D2.2 (A), D3.2 (A), D4.1 (K), D5.1 (K), J1.2, J1.3, J2.1, J3.1, J4.1, J5.1, J6.1, J8.1, J10.5, J10.6, J12.1, J13.1, J14.6, J14.9, J14.20, J14.25, J14.30, J14.34, J14.39, J17.2, J18.2, J19.2, J22.2, J23.2, J24.2, Q1.3 (E), U1.3 (GND), U1.5 (~ON/OFF), U2.3 (GND), U2.5 (~ON/OFF)
unnamed: A1.17 (3V3), R4.2
unnamed: D1.2 (A), R1.2
unnamed: D2.1 (K), L1.1, U1.2 (OUT)
unnamed: D3.1 (K), L2.1, U2.2 (OUT)
unnamed: D4.2 (A), R2.2
unnamed: D5.2 (A), R3.2
unnamed: F1.1, J1.1
unnamed: J11.1, Q1.2 (C)

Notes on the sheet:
A4-SDA-P23 A5-SCL-P24
Limit switch 2
Jumpers for stepping modes
Project Hayley V3
Limit switches / Potentiometers
Miscellaneous I2C, Power Supply, Fan etc
CR0805-JW-103ELF
D0-RX-P2 D1-TX-P1
All 0.1 uF - C0805C104K5RAC7800 All 470 uF - 477CKE035M
CR0805-FX-1000ELF
Axis 4
BUL7216 TO-220 NPN, 3A
Axis 1
Limit switch 1
Limit switch 6
CR0805-FX-4990ELF
Limit switch 4
Servos
Limit switch 5
LSM0805463V
Stepper mode settings
EN - low = enabled (keep low) SLP - low = sleep (keep high) RST - low = rest & home (keep high)
Axis 6
Transitor
LSM0805412V
LED Strip
RGEF1000-2
Spare Power Pins
Spares
I2C & 5V
Limit switch 3
Axis 2
12V Fan
Spare pins
Nano 33 IoT
Dual 12V to 5V buck switching regulators
Jumpers for RST, SLP, EN
Axis 5
Axis 3
12 V supply, at least 120 W

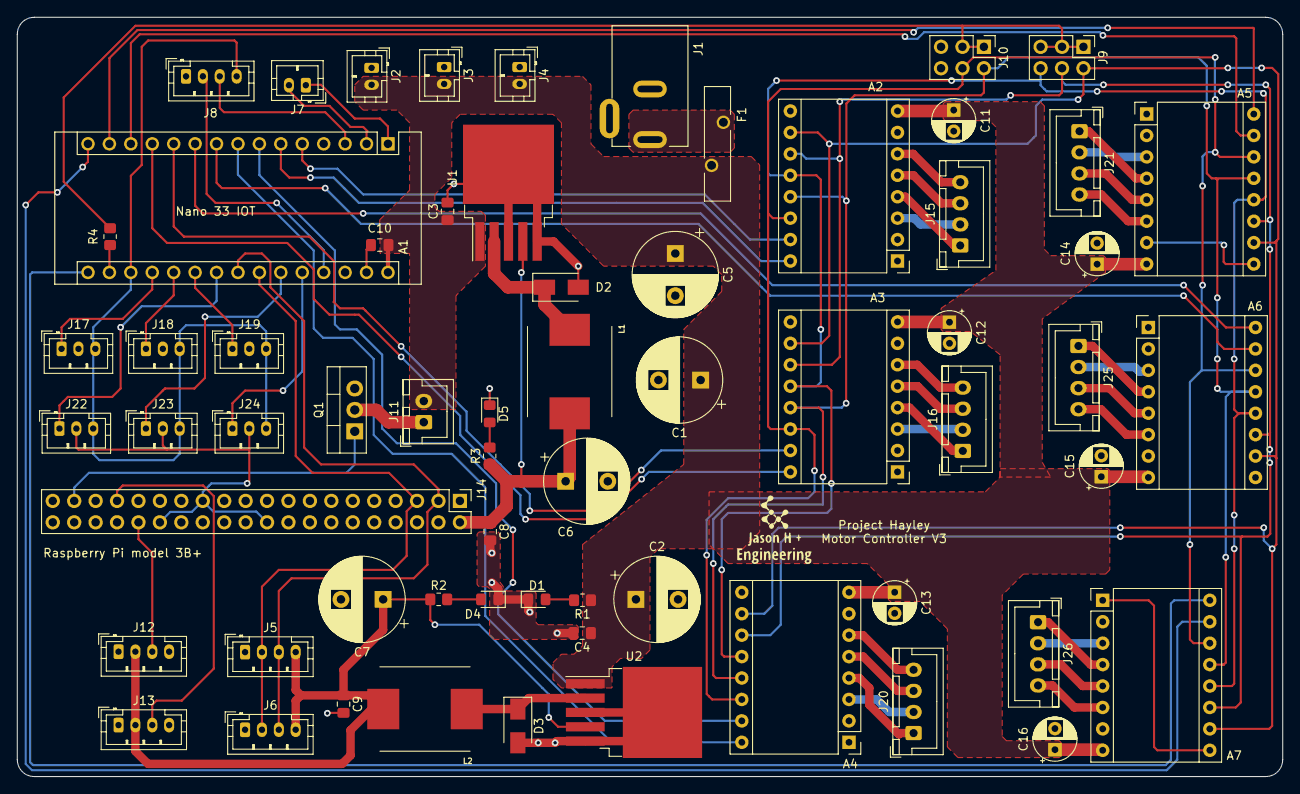
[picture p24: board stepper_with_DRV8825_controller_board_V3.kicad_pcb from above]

Board: 2 copper layers, 150.0 x 90.0 mm, 64 parts (0 on the bottom side), 70 nets.

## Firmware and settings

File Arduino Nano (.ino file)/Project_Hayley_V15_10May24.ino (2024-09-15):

/*

V9 - new baseline for controller V3 (purple board) + CNC machined arm
V10 - use pointers and add functions to optimize/shorten code
V11 - stepper.setSpeed() to move all linkages start/stop within fixed time
V13 - stepper 2 direction updated with a new stronger stepper motor
V14 - unknown
V15 - workaround to use original Axis 6 driver on Axis 5 (troubleshoot A5 cannot move) 

*/

// Pins for Motor Controller 

#include <Wire.h>
#include <AccelStepper.h>

// START DEFINE SECTION FOR MOTOR CONTROLLER V3
#define SLAVE_ADDRESS 0x04 // Nano IoT 2

// Define pin connections
#define stepper_1_stepPin 2
#define stepper_1_dirPin 3

#define stepper_2_stepPin 8
#define stepper_2_dirPin 9

#define stepper_3_stepPin 4
#define stepper_3_dirPin 5

#define stepper_4_stepPin 10
#define stepper_4_dirPin 11

// #define stepper_5_stepPin 6
// #define stepper_5_dirPin 7

// #define stepper_6_stepPin 12
// #define stepper_6_dirPin 13

#define stepper_5_stepPin 12
#define stepper_5_dirPin 13

#define stepper_6_stepPin 6
#define stepper_6_dirPin 7


// Define motor interface type
#define motorInterfaceType 1 //AccelStepper::DRIVER (1) means a stepper driver (with Step and Direction pins)
#define no_of_steppers 6
#define max_speed 3000
#define motor_acceleration 60000.0
#define micro_step 4 //e.g. half stepping = 2 

// #define RST_SLP_Pin 10 // do not need for controller V3
// #define enable_Pin 11 //KIV, setting high will off motor holding current

/*#define limitswitch1 14 //analog A0
#define limitswitch2 15 //analog A1
#define limitswitch3 16 //analog A2
#define limitswitch4 17 //analog A3
#define limitswitch5 20 //analog A6
#define limitswitch6 21 //analog A7*/

static int limitswitch1 = 14; //analog A0
static int limitswitch2 = 15; //analog A1
static int limitswitch3 = 16; //analog A2
static int limitswitch4 = 17; //analog A3
static int limitswitch5 = 20; //analog A6
static int limitswitch6 = 21; //analog A7

static int axis_1_start_pos = 3050*micro_step;
static int axis_2_start_pos = 1300*micro_step;
static int axis_3_start_pos = -1200*micro_step;
static int axis_4_start_pos = 2700*micro_step;
static int axis_5_start_pos = 1400*micro_step;
static int axis_6_start_pos = 0*micro_step;

/*#define axis_1_start_pos 10
#define axis_2_start_pos 10
#define axis_3_start_pos 10
#define axis_4_start_pos 10
#define axis_5_start_pos 10
#define axis_6_start_pos 10*/

//#define limit_switch_activated_steps 100 //stepper steps to take when limit switch activated

static int direction[no_of_steppers] = {-1, -1, 1, -1, -1, -1};

//int* limitswitch_vararray[no_of_steppers] = {&limitswitch1, &limitswitch2, &limitswitch3, &limitswitch4, &limitswitch5, &limitswitch6};

//define an array of stepper pointers. initialize the pointer to NULL (null pointer) for safety (see below)
AccelStepper *steppers[no_of_steppers] = {NULL, NULL, NULL, NULL, NULL, NULL};

// END DEFINE SECTION FOR MOTOR CONTROLLER V2


bool flag = false;
//static bool limit_flag = true;
static int zero_flag = 0;
  
//bool homingComplete = false;

// pointers for boolean state of stepper_x_Home
static bool stepper_1_Home, stepper_2_Home, stepper_3_Home, stepper_4_Home, stepper_5_Home, stepper_6_Home;
static bool* stepper_Home_vararray[no_of_steppers] = {&stepper_1_Home, &stepper_2_Home, &stepper_3_Home, &stepper_4_Home, &stepper_5_Home, &stepper_6_Home};

// pointers for limitswitchx pin numbers
static int* limitswitch_vararray[no_of_steppers] = {&limitswitch1, &limitswitch2, &limitswitch3, &limitswitch4, &limitswitch5, &limitswitch6};

// pointers for each axis home position (steps from limit switch activation)
static int* axis_start_pos_vararray[no_of_steppers] = {&axis_1_start_pos, &axis_2_start_pos, &axis_3_start_pos, &axis_4_start_pos, &axis_5_start_pos, &axis_6_start_pos};

// https://medium.com/@sandhan.sarma/sending-floats-over-the-i2c-bus-between-two-arduinos-part-2-486db6dc479f
union BytesToFloat {
    // 'converts' incoming bytes to long array
    byte valueBuffer[no_of_steppers*8];
    long valueReading[no_of_steppers];    
} converter;

union BytesToInt {
    // 'converts' incoming bytes to a single char
    // byte IntBuffer[1*8];
    // long IntReading[1]; 
    byte IntBuffer[8];
    long  IntReading[1];    
} convert_int;

struct dataStruct {
   long motor_1_stepper_position;          
   long motor_2_stepper_position;  
   long motor_3_stepper_position;          
   long motor_4_stepper_position;          
   long motor_5_stepper_position; 
   long motor_6_stepper_position; 
   long zero_status;
} stepper_position_data; 

void setup() {
  
  
  for (int x = 0; x <= 5; x++) {
    *stepper_Home_vararray[x] = false; // set all stepper_x_Home to false
    pinMode(*limitswitch_vararray[x], INPUT_PULLUP); // set all limitswitchx to internal pullup
  }
  
  // Create stepper instances
  steppers[0] = new AccelStepper(motorInterfaceType, stepper_1_stepPin, stepper_1_dirPin);
  steppers[1] = new AccelStepper(motorInterfaceType, stepper_2_stepPin, stepper_2_dirPin);
  steppers[2] = new AccelStepper(motorInterfaceType, stepper_3_stepPin, stepper_3_dirPin);
  steppers[3] = new AccelStepper(motorInterfaceType, stepper_4_stepPin, stepper_4_dirPin);
  steppers[4] = new AccelStepper(motorInterfaceType, stepper_5_stepPin, stepper_5_dirPin);
  steppers[5] = new AccelStepper(motorInterfaceType, stepper_6_stepPin, stepper_6_dirPin);
  
  Serial.begin(9600);          // start serial for output
  delay(100);
  Wire.begin(SLAVE_ADDRESS);   // initialize i2c as slave
  Wire.onReceive(receiveData); // receive interrupt callback (triggered by I2C-Master)
  Wire.onRequest(sendData);
  Serial.println("Ready!");
    

  for (int i = 0; i <= 5; i++) {
    steppers[i]->setMaxSpeed(max_speed); //steps per second
    steppers[i]->setAcceleration(motor_acceleration); //desired acceleration in steps per second per second
  }
  
  zero_flag = 0;
  zero_stepper();

}


void loop() {

    if(flag) run_stepper();
    
    for (int i = 0; i <= 5; i++) {
      steppers[i]->run();
    }
    
    limit_switch_checks();
    
    stepper_position_data.motor_1_stepper_position = steppers[0]->currentPosition();
    stepper_position_data.motor_2_stepper_position = steppers[1]->currentPosition();
    stepper_position_data.motor_3_stepper_position = steppers[2]->currentPosition();
    stepper_position_data.motor_4_stepper_position = steppers[3]->currentPosition();
    stepper_position_data.motor_5_stepper_position = steppers[4]->currentPosition();
    stepper_position_data.motor_6_stepper_position = steppers[5]->currentPosition();
    stepper_position_data.zero_status = zero_flag;
    
    //if ((steppers[0]->distanceToGo()!=0) || (steppers[1]->distanceToGo()!=0) || (steppers[2]->distanceToGo()!=0) || (steppers[3]->distanceToGo()!=0) || (steppers[4]->distanceToGo()!=0)) {
      
/*      for (int x = 0; x < no_of_steppers; x++) {
        Serial.println((String)"Motor "+x+" steps remaining: "+steppers[x]->distanceToGo());
      }*/
      //Serial.println((String)"Motor 0 steps remaining: "+steppers[0]->distanceToGo());
    //}



}


void zero_stepper(){
  
  // reset all stepper_x_Home to false when this function is called
  for (int x = 0; x <= 5; x++) {
    *stepper_Home_vararray[x] = false;
  }
  
  // reset to max_speed
  for (int i = 0; i <= 5; i++) {
    steppers[i]->setMaxSpeed(max_speed); //steps per second
    steppers[i]->setAcceleration(motor_acceleration); //desired acceleration in steps per second per second
  }
  
  stepper_6_Home = true; // for the moment, I am not using limit switch on axis 6
    
while((stepper_1_Home == false) || (stepper_2_Home == false) || (stepper_3_Home == false) || (stepper_4_Home == false) || (stepper_5_Home == false) || (stepper_6_Home == false)) {

  for (int x = 0; x <= 5; x++) {

    if ((digitalRead(*limitswitch_vararray[x]) == HIGH) && (*stepper_Home_vararray[x] == false)) {
      steppers[x]->move(10*direction[x]);
    }
    else {
        *stepper_Home_vararray[x] = true;
        if (digitalRead(*limitswitch_vararray[x]) == LOW) { 
          steppers[x]->move(-400*direction[x]); 
        }
     }
     
      steppers[x]->run();
    
    }
    Serial.println("Homing!");
  }
  delay(1000);
  Serial.println("Homed!");
  
  for (int x = 0; x <= 5; x++) {
    steppers[x]->move(*axis_start_pos_vararray[x]); 
  }


/*  steppers[0]->move(axis_1_start_pos); 
  steppers[1]->move(axis_2_start_pos); 
  steppers[2]->move(axis_3_start_pos); 
  steppers[3]->move(axis_4_start_pos); 
  steppers[4]->move(axis_5_start_pos); 
  steppers[5]->move(axis_6_start_pos); */

  while ((steppers[0]->distanceToGo() != 0) || (steppers[1]->distanceToGo() != 0) || (steppers[2]->distanceToGo() != 0) || (steppers[3]->distanceToGo() != 0) || (steppers[4]->distanceToGo() != 0) || (steppers[5]->distanceToGo() != 0)) {
    for (int i = 0; i <= 5; i++) {
      steppers[i]->run();
      
/*      if ((i == 0) || (i == 3)) {
        Serial.print("steppers[0]->distanceToGo(): ");
        Serial.println(steppers[0]->distanceToGo());
        Serial.print("steppers[3]->distanceToGo(): ");
        Serial.println(steppers[3]->distanceToGo());
      } */
    }
  }
  
  for (int i = 0; i <= 5; i++) {
    steppers[i]->setCurrentPosition(0);
  }
    
  zero_flag = 1;
  
}


void limit_switch_checks(){
  
for (int x = 0; x <= 5; x++) {
 
    if (digitalRead(*limitswitch_vararray[x]) == LOW) {
      steppers[x]->move(-100*direction[x]);
    }
    
    
  }

}

void run_stepper(){
  
  long motor_steps[no_of_steppers]; 
  float time_travel = 1.0;
  bool speed_flag[no_of_steppers] = {false, false, false, false, false, false};
  // sort and find the shortest time possible
  
 
  for (int x = 0; x < no_of_steppers; x++) {
    
    motor_steps[x] = converter.valueReading[x];
    
    while (speed_flag[x]!= true) {
    
    //Serial.println((String)"Motor "+x+" steps is: "+motor_steps[x]);
    //steppers[x]->move(motor_steps[x]);
    //float stepper_speed = motor_steps[x]/4.0;
    //steppers[x]->moveTo(motor_steps[x]);
      float set_speed = (motor_steps[x] - (steppers[x]->currentPosition()))/time_travel;
      if ((set_speed < 2000.0) && (set_speed > -2000.0)) {
        speed_flag[x] = true;}
      else {
        time_travel+=0.1; //add time travel allowed
      }  
    //if (set_speed < -4000.0) {set_speed = -max_speed;}
    //steppers[x]->setMaxSpeed(set_speed); // first trial, set all movement to 8 seconds

    }
  
  }
    
    Serial.println((String)"Time travel allowed is: "+time_travel);

  
  for (int x = 0; x < no_of_steppers; x++) {
    
    motor_steps[x] = converter.valueReading[x];
    Serial.println((String)"Motor "+x+" steps is: "+motor_steps[x]);
    //steppers[x]->move(motor_steps[x]);
    //float stepper_speed = motor_steps[x]/4.0;
    steppers[x]->moveTo(motor_steps[x]);
    float set_speed = (motor_steps[x] - (steppers[x]->currentPosition()))/time_travel;
    //if (set_speed > 2000.0) {set_speed = max_speed;}
    //if (set_speed < -2000.0) {set_speed = -max_speed;}
    steppers[x]->setMaxSpeed(set_speed); // first trial, set all movement to 8 seconds
    Serial.println((String)"Motor "+x+" speed is: "+set_speed);
  }
  
    flag = false;
    
}

void receiveData(int byteCount){
  
  // hint for not triggering onreceive accidentally by onrequest 
  // https://forum.arduino.cc/t/raspberrypi-i2c-arduino-onreceive-onrequest-collision/321731/3
    Serial.println("byteCount recieved");
    Serial.println(byteCount);
  
    if (byteCount>6){
      
      Serial.println("stepper triggered");
      for(uint8_t index = 0; index<byteCount; index++){
          converter.valueBuffer[index] = Wire.read();
      }
      
      flag = true;
      
    }
    
    if (byteCount<6){ // one integer from python is 4 bytes, but an additional dummy byte make it 5 in total
      
      // Serial.println(byteCount);
      for(uint8_t index = 0; index<byteCount; index++){
          convert_int.IntBuffer[index] = Wire.read();
          //Serial.println(convert_int.IntBuffer[index]);
      }
      
      //Serial.println(convert_int.IntReading[0]);

      if (convert_int.IntReading[0] == 8){
        Serial.println("stepper recalibration triggered");
        zero_flag = 0;
        zero_stepper();
      }
      

    }
    
    
}

// test reference from https://stackoverflow.com/questions/40196733/how-to-pass-arduino-struct-to-raspberry-pi-via-i2c

void sendData(){
  
  Wire.write((byte *)&stepper_position_data, sizeof(stepper_position_data));
  flag = false;

}

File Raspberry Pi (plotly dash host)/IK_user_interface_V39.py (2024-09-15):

# -*- coding: utf-8 -*-
"""

V31 Baseline for Project Hayley V2 
V32 New linkages for Project Hayley V3
V33 Add dash page to process IK solved points and path from CSV
V34 Tidy up the HTML portion, further work on added dash page for IK path plan
V39 Update to handle CSV file - auto locate theta columns  

"""

import dash
from dash import dcc
from dash import html
import plotly.express as px
import plotly.graph_objs as go
import pandas as pd
import numpy as np
import smbus2 as smbus
import struct
import time
import math
from skspatial.objects import Plane, Point, Vector
import base64
import io
from dash import dash_table
import subprocess

# device address
arduino_IOT = 0x04

# initialize serial commumication
bus = smbus.SMBus(1)
time.sleep(1)

angle_slider_resolution = 0.1 # degrees


gear_reduction = [-30, -30, 30, -30, 30, 30] #-ve sign to flip direction of physical motor
steps_per_rotation = [200, 200, 200, 200, 200, 200]
micro_steps = [4, 4, 4, 4, 4, 4]

hinge_length = 14 # for illustrating the axis hinge in 3d view
max_iter = 500 # iterations allow for IK CCD
err_min = 2.5 # acceptable error in mm in inverse kinematics calculation

figure_axis_limit = 500

# config file to limit the max min angles of the axis
config_df = pd.read_csv('config - project Hayley V3.csv')
lower_limit = list(config_df["Absolute low angle limit"])
upper_limit = list(config_df["Absolute high angle limit"])

start_angles_list = list(config_df["Start angle"])
angles_list = start_angles_list.copy()

list_of_thetas = [0] * 32 # To be updated

index_of_angles = [2, 9, 12, 17, 23, 29] #hinge for project Hayley v3
#index_of_angles = [2, 9, 11, 16, 22, 28] #hinge 
index_of_hinges = index_of_angles.copy()

angle_max = list_of_thetas.copy()
angle_min = list_of_thetas.copy()
list_of_blockers = list_of_thetas.copy()

# [link number, theta about Z, alpha about X, d in Z direction, a or r in X direction]
# Link Length Parameter
# this is Project Hayley V3 linkage
local_linkage_data = [
    [0,0,0,0,0], #0
    [1,0,0,54,0], #1 
    [1,0,0,0,0], #theta_1 - Axis1, anti-clockwise with positive theta #2
    [2,0,-90,0,0], #3
    [2,0,0,35,0], #4 
    [2,0,90,0,0], #5
    [2,0,0,35.5,0], #6
    [2,0,90,0,0], #7
    [2,90,0,0,0], #8
    [2,0,0,0,0], #theta_2 - Axis2, down with positive theta #9
    [2,0,-180,0,0], #10
    [3,0,0,0,60], #11    
    [3,0,0,0,0], #theta_3 - Axis3, down with positive theta #12
    [4,0,0,0,33],     #13
    [4,0,0,-34.5,0],  # from here, switch between X and Z axis #14
    [4,90,0,0,0],     #15
    [4,0,90,0,0],     #16
    [4,0,0,0,0], #theta_4 - Axis4, anti-clockwise from top view with positive theta  #17
    [5,0,0,54,0], #18
    [5,0,-90,0,0],     #19
    [5,-90,0,0,0],     #20
    [5,0,0,32,0], #21
    [5,0,0,0,29],  # from here, switch between X and Z axis #22
    [5,0,0,0,0], #theta_5 - Axis5, down with positive theta #23
    [6,0,0,0,47],#24
    [6,0,0,-32,0], #25
    [6,0,0,0,25], #26
    [6,90,0,0,0],     #27
    [6,0,90,0,0],     #28    
    [6,0,0,0,0], #theta_6 - Axis6, anti-clockwise with positive theta #29
    [7,0,0,22,0], # dummy 20 mm extension #30
    [7,0,-90,0,0], # dummy 20 mm extension #31
    [7,-90,0,0,0], # dummy 20 mm extension #32
    ]


list_of_thetas = [0] * len(local_linkage_data)
angle_max = list_of_thetas.copy()
angle_min = list_of_thetas.copy()
list_of_blockers = list_of_thetas.copy()

for i, value in enumerate(index_of_angles):
    angle_max[value] = upper_limit[i]
    angle_min[value] = lower_limit[i]
    list_of_blockers[value] = 1
    

# special provision for the blockers to have theta to rotate the coodinate frame that is not due to hinge i.e theta due to mechanical link
for i, linkage in enumerate(local_linkage_data):
    if linkage[1] != 0:
        list_of_blockers[i] = 2
        list_of_thetas[i] = local_linkage_data[i][1]
        


def check_list(input_list):
    lower_exceed_count = 0
    upper_exceed_count = 0
    for i in range(len(input_list)):
        if input_list[i] < lower_limit[i]: lower_exceed_count=lower_exceed_count+1
        if input_list[i] > upper_limit[i]: upper_exceed_count=upper_exceed_count+1
    
    if lower_exceed_count>0 or upper_exceed_count>0: 
        return_string = "Angles out of range"
    else:
        return_string = "Angles in range"        

    return return_string


def DH_matrix(theta, alpha, delta, rho):

    transient_matrix = np.eye(4)
    
    # Handle DH parameters, row-by-row, left-to-right
    transient_matrix[0,0]=np.cos(theta/180*np.pi)
    transient_matrix[0,1]=-np.sin(theta/180*np.pi)    
    transient_matrix[0,2]=0    
    transient_matrix[0,3]=rho    

    transient_matrix[1,0]=np.sin(theta/180*np.pi)*np.cos(alpha/180*np.pi)
    transient_matrix[1,1]=np.cos(theta/180*np.pi)*np.cos(alpha/180*np.pi)  
    transient_matrix[1,2]=-np.sin(alpha/180*np.pi)     
    transient_matrix[1,3]=-np.sin(alpha/180*np.pi) * delta    

    transient_matrix[2,0]=np.sin(theta/180*np.pi)*np.sin(alpha/180*np.pi)
    transient_matrix[2,1]=np.cos(theta/180*np.pi)*np.sin(alpha/180*np.pi)  
    transient_matrix[2,2]=np.cos(alpha/180*np.pi)     
    transient_matrix[2,3]=np.cos(alpha/180*np.pi) * delta   

    return transient_matrix

def get_closest_coordinate_params(quadrant_coordinates_df):
    
    closest_coordinate = quadrant_coordinates_df[quadrant_coordinates_df['distance'] == quadrant_coordinates_df['distance'].min()]

    return(closest_coordinate)


def input_linkage_angles(list_of_thetas):
    
    for i in range(len(list_of_thetas)):
        # if list_of_blockers[i] == 2: # This is for special provision at axis 5
        #     list_of_thetas[i] = 90
        local_linkage_data[i][1] = list_of_thetas[i]

    array_matrix = []
    transformation_matrix = None
    
    for i, linkage in enumerate(local_linkage_data):
        
        # Rotations first
        transient_rotation = DH_matrix(linkage[1], linkage[2], 0, 0)
        
        if transformation_matrix is None:
            transformation_matrix = transient_rotation
        else:
            transformation_matrix = np.matmul(transformation_matrix, transient_rotation)
        
        # then the translations
        transient_translation = DH_matrix(0, 0, linkage[3], linkage[4])
        
        if transformation_matrix is None:
            transformation_matrix = transient_translation
        else:
            transformation_matrix = np.matmul(transformation_matrix, transient_translation)
        
        array_matrix.append(transformation_matrix)

    return(array_matrix)


def sqrt_sum_aquare(input_list):
    sum_square = 0
    for value in input_list:
        sum_square += value*value
    return(math.sqrt(sum_square))
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

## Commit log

2024-09-14 Initial Upload
    Partial upload only - appending more files
    [Part 10.step, Part 12.step, Part 13.step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]
2024-09-15 Second upload for python and .ino files
    "Raspberry Pi (plotly dash host)" to be copied to raspberry Pi 3/4 and run "IK_user_interface_V39.py"
    "Project_Hayley_V15_10May24" to be run on a Arduino nano 33 IoT/BLE, which is in turn mounted on adaptor board - see schematics "Adaptor Board (schema, gerbers, kicad project folder)"
    [config - project Hayley V3.csv]
2024-09-15 Update README.md
    Added table to explain contents. Added placeholder for inverse kinematics solver.
